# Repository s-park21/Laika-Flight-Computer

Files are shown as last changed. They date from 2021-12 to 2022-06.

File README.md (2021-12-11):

# Liaka-Flight-Computer
Kicad files for the Liaka flight computer

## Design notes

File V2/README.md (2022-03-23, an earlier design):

# Liaka-Flight-Computer
Kicad PCB files for the Liaka flight computer

PCB Ordering Information:

Export the PCB files as Gerber. See online tutorial for details. Upload drill files, gerber files, BOM and .pos file to JLCPCB for PCB manufacture and assembly. 
JLC can assemble most of the components other than RFM95W, GPS, Baro and various other minor parts. I highly reccomend to have JLC assemble the ESP32 chip for you.

For code to run on the board, see my rocket-software repository.

Errata List:

- PWR and GND for XT-30 connector are reversed. 
- Round edges of PCB to minimise stress concentrations.

Areas for improvement:
- MPU6050 locks out after 15g. Consider higher range accelerometer.
- Consider the use of a flash chip rather than a micro SD card.

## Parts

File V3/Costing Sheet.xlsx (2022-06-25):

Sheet: Sheet1
Comment | Designator | Footprint | LCSC | Mouser | Digikey | Cost Each (AUD) | USD to AUD Rate
100nF | C1,C2,C4,C13,C16 | Capacitor_SMD:C_0603_1608Metric | C14663 |  |  | PCB inc. | 1.42
1uF | C11,C12 | Capacitor_SMD:C_0603_1608Metric | C15849 |  |  | PCB inc.
10nF | C17 | Capacitor_SMD:C_0603_1608Metric | C57112 |  |  | PCB inc.
0.1uF | C7,C10,C18,C20 | Capacitor_SMD:C_0603_1608Metric | C14663 |  |  | PCB inc.
2.2nF | C19 | Capacitor_SMD:C_0603_1608Metric | C1604 |  |  | PCB inc.
10uF | C3,C5,C9,C14 | Capacitor_SMD:C_0603_1608Metric | C19702 |  |  | PCB inc.
10uF | C6 | Capacitor_Tantalum_SMD:CP_EIA-3216-18_Kemet-A | C8545 |  |  | PCB inc.
100uF | C8,C15 | Capacitor_Tantalum_SMD:CP_EIA-3528-21_Kemet-B | C16133 |  |  | PCB inc.
LED_BLUE | D1 | LED_SMD:LED_0603_1608Metric | C72041 |  |  | PCB inc.
B5819W | D2,D3,D4 | Diode_SMD:D_SOD-123 | C8598 |  |  | PCB inc.
ERROR_STATUS_LED | D5 | LED_SMD:LED_0603_1608Metric | C2286 |  |  | PCB inc.
LED_RED | D6 | LED_SMD:LED_0603_1608Metric | C72043 |  |  | PCB inc.
XTSD04GLGEAG | IC1 | SON127P800X600X95-8N | C558839 |  |  | 6.07902
Conn_Coaxial | J1 | Connector_Coaxial:SMA_Amphenol_132291_Vertical | C504007 |  |  | 0.63261
2-3S_LiPo_LARGE_HOLE_XT-30 | J2 | Connector_AMASS:AMASS_XT30PW-M_1x02_P2.50mm_Horizontal
USB_B_Micro | J5 | Connector_USB:USB_Micro-B_Molex-105017-0001 | C132563 |  |  | 2.4424
THD2528-11SD-GF | J7 | Local_footprints:THD252811SDGF | C283232 |  |  | 0.30743
SMT-1127-S-R | LS1 | XDCR_SMT-1127-S-R |  | 665-SMT1127SR |  | 2.17
Si2301CDS | Q1,Q2,Q3 | Package_TO_SOT_SMD:SOT-23 | C10487 |  |  | PCB inc.
MMBT2222 | Q4,Q5 | Package_TO_SOT_SMD:SOT-23 | C8512 |  |  | PCB inc.
2N7002 | Q6 | Package_TO_SOT_SMD:SOT-23 | C8545 |  |  | PCB inc.
1k | R1,R13,R14,R18 | Resistor_SMD:R_0603_1608Metric | C21190 |  |  | PCB inc.
12k | R10,R11 | Resistor_SMD:R_0603_1608Metric | C22790 |  |  | PCB inc.
10k | R12,R15,R21 | Resistor_SMD:R_0603_1608Metric | C25804 |  |  | PCB inc.
2.4k | R16,R17 | Resistor_SMD:R_0603_1608Metric | C22940 |  |  | PCB inc.
300k | R19 | Resistor_SMD:R_0603_1608Metric | C23024 |  |  | PCB inc.
50k | R2 | Resistor_SMD:R_0603_1608Metric | C23206 |  |  | PCB inc.
5.1M | R3 | Resistor_SMD:R_0603_1608Metric | C13320 |  |  | PCB inc.
3M | R4,R6 | Resistor_SMD:R_0603_1608Metric | C23156 |  |  | PCB inc.
100k | R5,R8,R9,R20 | Resistor_SMD:R_0603_1608Metric | C25803 |  |  | PCB inc.
1M | R7 | Resistor_SMD:R_0603_1608Metric | C22935 |  |  | PCB inc.
SW_SPDT | SW1 | Local_footprints:SSSS811101 | C109335 |  |  | PCB inc.
RST | SW2 | Button_Switch_SMD:SW_Push_1P1T_NO_CK_KSC6xxJ | C318884 |  |  | PCB inc.
BOOT | SW3 | Button_Switch_SMD:SW_Push_1P1T_NO_CK_KSC6xxJ | C318884 |  |  | PCB inc.
SD_DUMP | SW4 | Button_Switch_SMD:SW_Push_1P1T_NO_CK_KSC6xxJ | C318884 |  |  | PCB inc.
L80-M39 | U1 | Local_footprints:L80-M39 | C133488 |  |  | 25.0914
MPU-6050 | U10 | Local_footprints:MPU-6050 | C24112 |  |  | PCB inc.
MS561101BA03-50 | U2 | Local_footprints:MS561101BA03-50 |  |  | MS561101BA03-50 | 20.72
ADXL375BCCZ-RL7 | U3 | Local_footprints:ADXL375BCCZ-RL7 | C481898 |  |  | 24.4098
RFM95W-915S2 | U4 | RF_Module:HOPERF_RFM9XW_SMD | C2844473 |  |  | 8.48734
LM393 | U5 | Local_footprints:LM393DR2G | C7955 |  |  | 0.0994
ADR5040ARTZ-2.048 | U6 | Local_footprints:Analog_Devices-ADR5040ARTZ-REEL7-Level_C | C144273 |  |  | 1.444282
AMS1117-3.3 | U7 | Package_TO_SOT_SMD:SOT-223-3_TabPin2 | C6186 |  |  | PCB inc.
CP2102N-A01-GQFN28 | U8 | Package_DFN_QFN:QFN-28-1EP_5x5mm_P0.5mm_EP3.35x3.35mm | C6568 |  |  | PCB inc.
ESP32-WROOM-32 | U9 | RF_Module:ESP32-WROOM-32 | C82899 |  |  | PCB inc.
 |  |  | 5 Fully assembled boards
 |  |  |  | PCB Cost |  | 169.03
 |  |  |  | Other component costs |  | 459.41841
 |  |  |  | Total |  | 628.44841
 |  |  | 1 Fully assembled board + 4 partially assembled boards
 |  |  |  | PCB Cost |  | 169.03
 |  |  |  | Other component costs |  | 91.883682
 |  |  |  | Total |  | 260.913682

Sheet: Sheet2
Feature | Laika V2 | Laika V3
GPS | X | X
LoRa | X | X
SD Card | X | X
Flash memory chip |  | X
Accelerometer | X | X
Gyro | X | X
High G Accelerometer |  | X
Buzzer |  | X
Battery protection |  | X
Axes labelled on silk screen |  | X
Barometer | X | X
Can connect to RRC3 | X | X
Looks sexy AF | X | X

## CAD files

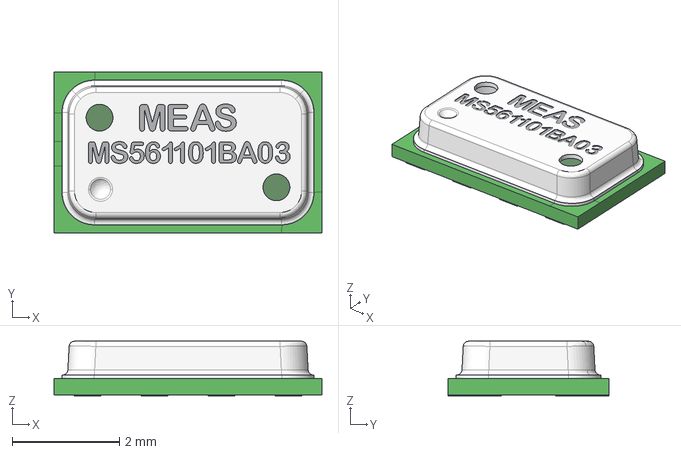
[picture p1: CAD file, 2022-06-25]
V3/Local Library/3D Models/MS5611-01BA03.stp
5.00 x 3.00 x 1.02 mm

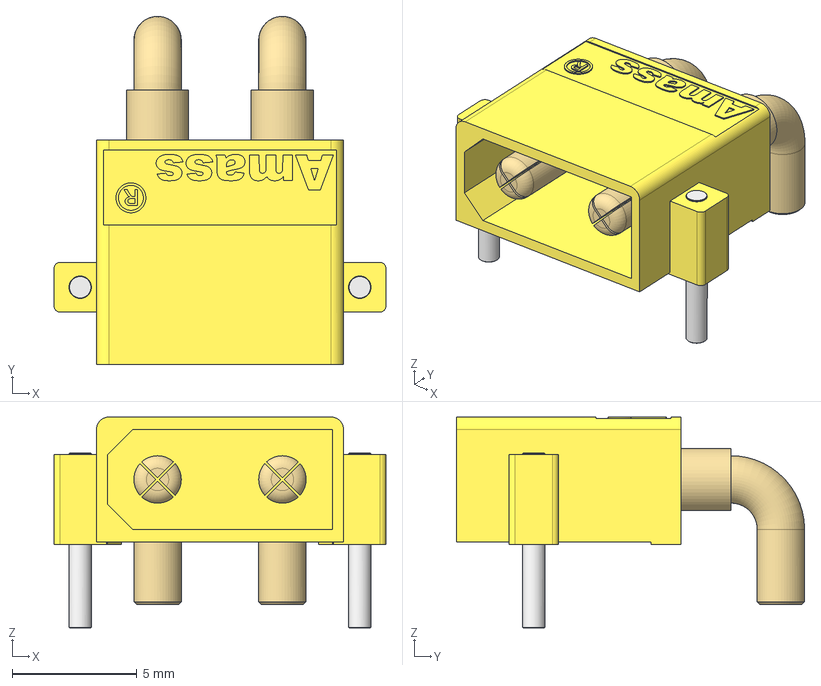
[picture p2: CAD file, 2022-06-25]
V3/Local Library/3D Models/Amass_XT30PW-M.stp
13.3 x 13.9 x 8.45 mm

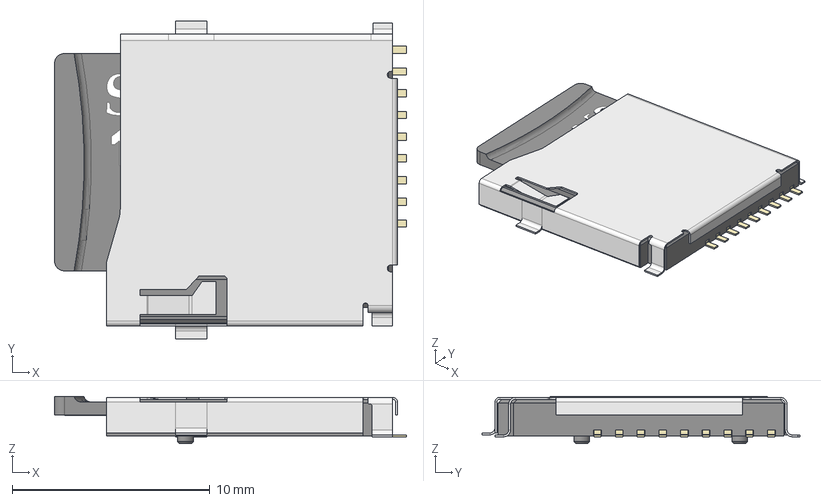
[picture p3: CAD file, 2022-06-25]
V3/Local Library/3D Models/THD2528-11SD-GF.stp.step
17.8 x 16.1 x 2.40 mm

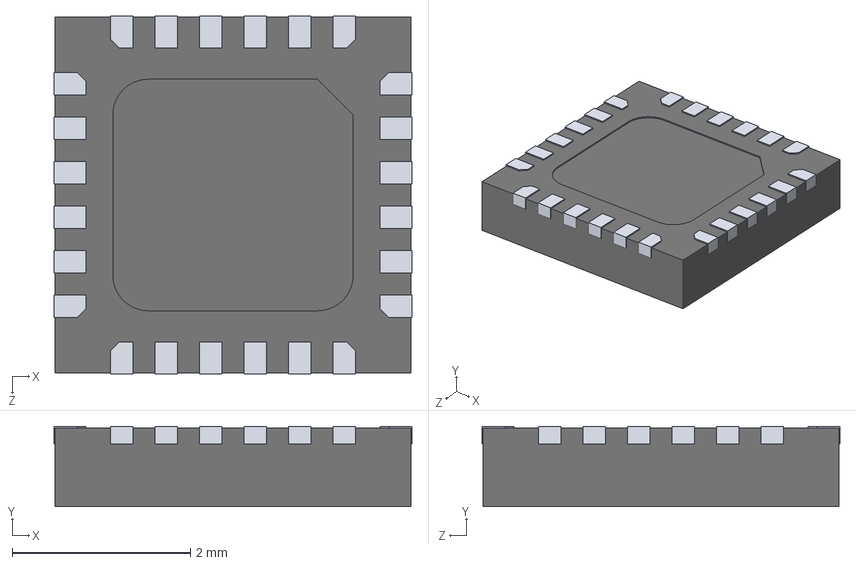
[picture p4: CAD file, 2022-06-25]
V3/Local Library/3D Models/MPU6050.STEP
4.02 x 0.9 x 4.02 mm

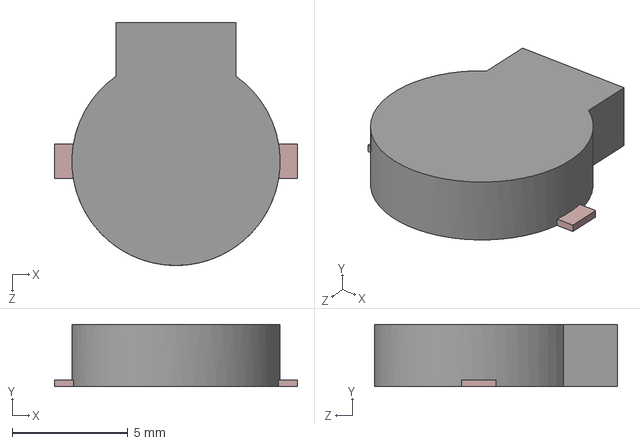
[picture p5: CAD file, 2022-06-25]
V3/Local Library/3D Models/SMT-1127-S-R.step
10.5 x 2.70 x 10.5 mm

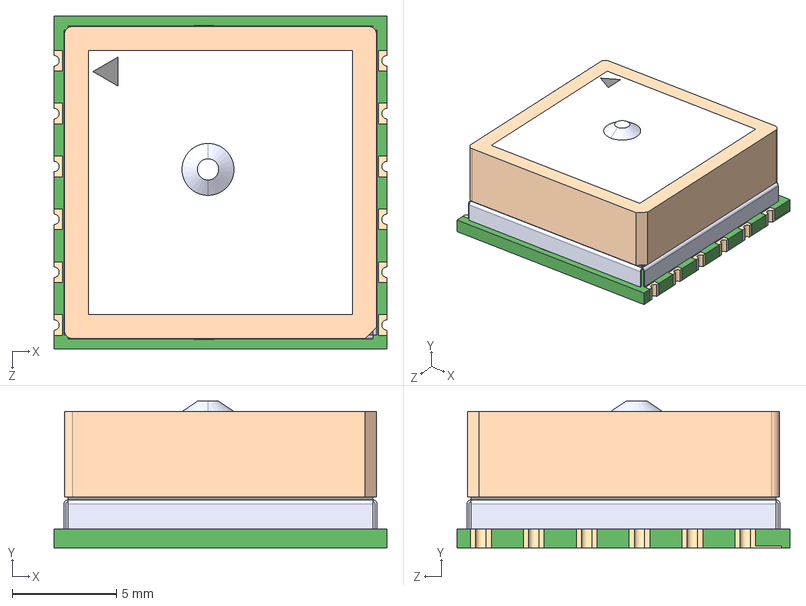
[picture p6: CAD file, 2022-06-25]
V3/Local Library/3D Models/L80-M39.STEP
16.0 x 7.05 x 16.0 mm

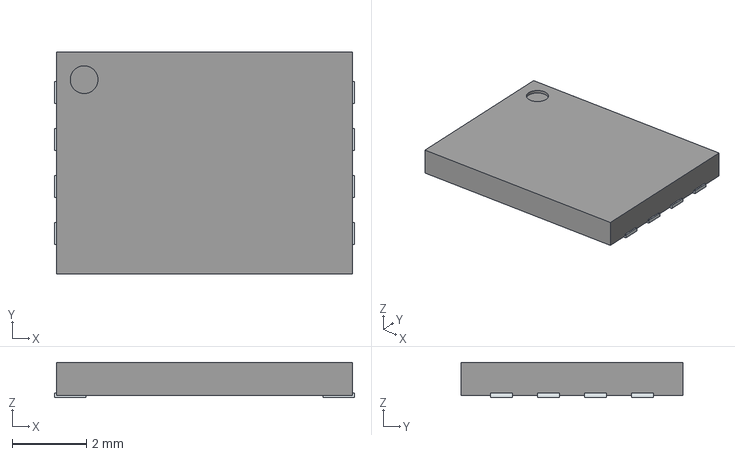
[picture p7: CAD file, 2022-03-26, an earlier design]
V2/Local Library/3D Models/XTSD04GLGEAG.stp
8.10 x 6.00 x 0.95 mm
PinsArrayLR

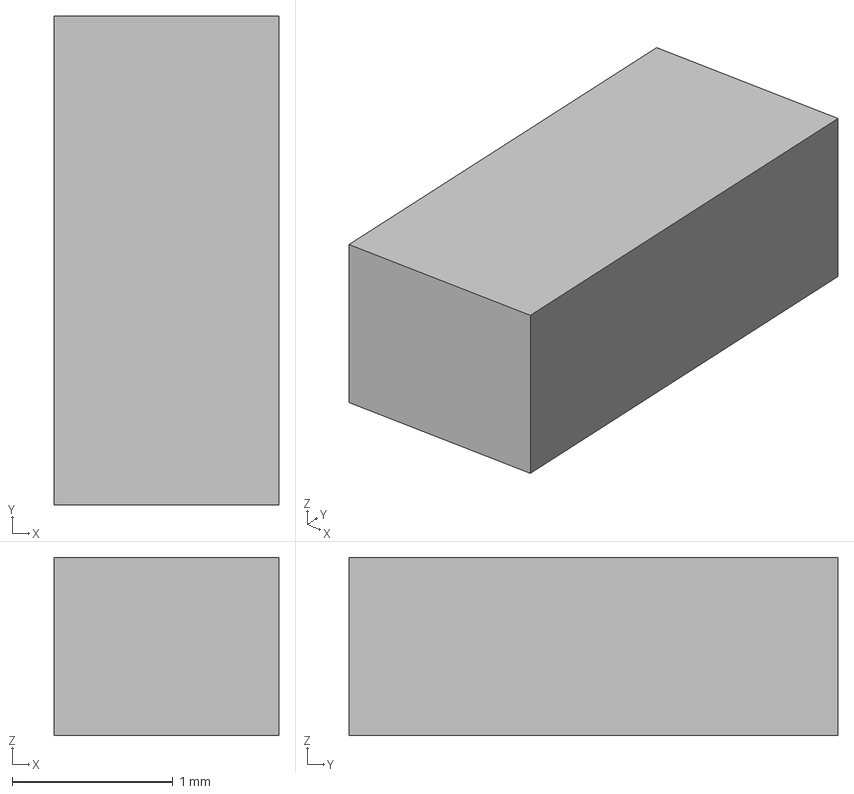
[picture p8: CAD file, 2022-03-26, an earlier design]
V2/Local Library/3D Models/Analog_Devices_-_ADR5040ARTZ-REEL7.step
1.40 x 3.04 x 1.11 mm

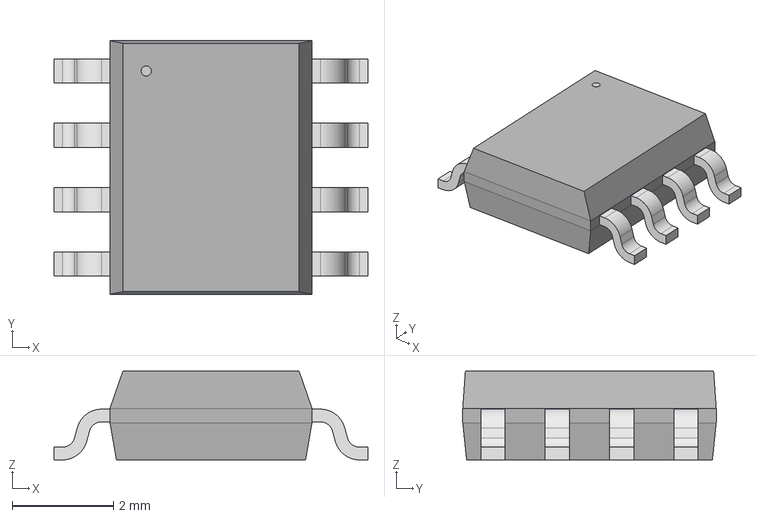
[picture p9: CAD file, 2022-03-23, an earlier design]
V2/Local Library/3D Models/SO_RMN6TP_STM.step
6.20 x 5.00 x 1.75 mm

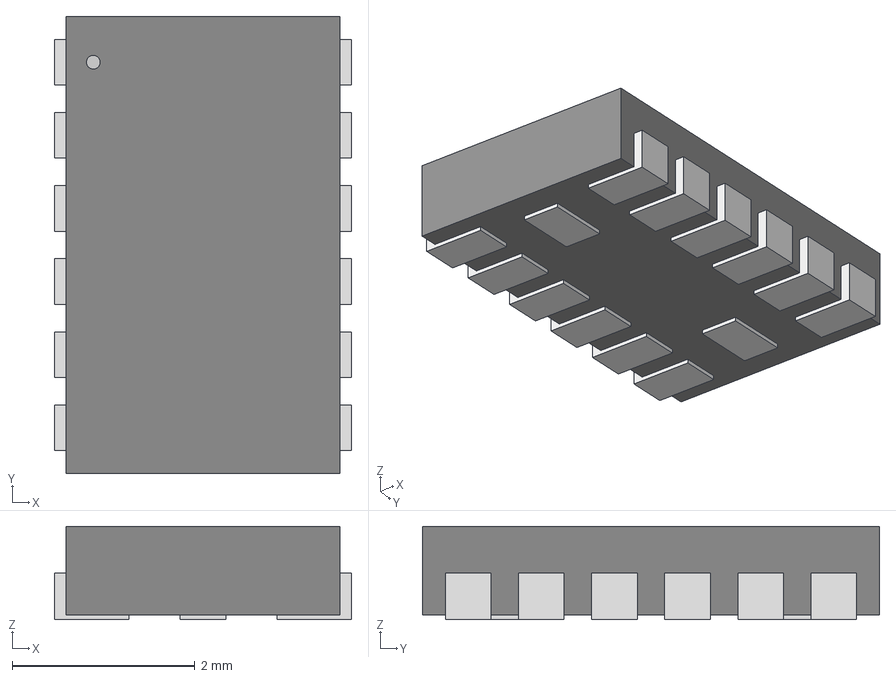
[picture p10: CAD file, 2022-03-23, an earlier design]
V2/Local Library/3D Models/LGA_CC-14-1_ADI.step
3.25 x 5.00 x 1.02 mm

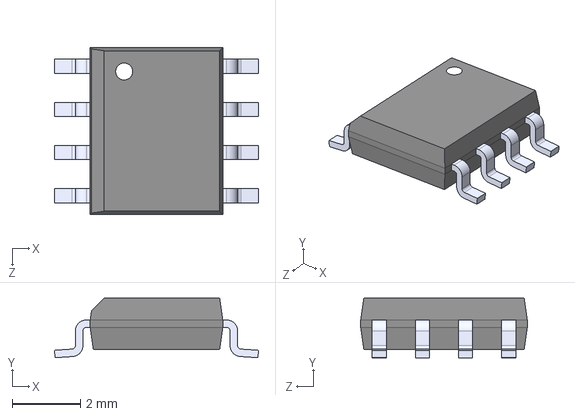
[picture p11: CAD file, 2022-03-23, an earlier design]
V2/Local Library/3D Models/SOIC127P600X175-8N.step
6.00 x 1.75 x 4.90 mm

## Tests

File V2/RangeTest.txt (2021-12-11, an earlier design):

Received packet '1886' with RSSI -23
Received packet '1918' with RSSI -47
Received packet '1949' with RSSI -48
Received packet '1980' with RSSI -48
Received packet '2043' with RSSI -49
Received packet '2074' with RSSI -48
Received packet '2106' with RSSI -48
Received packet '2137' with RSSI -47
Received packet '2200' with RSSI -23
Received packet '2231' with RSSI -22
Received packet '2262' with RSSI -19
Received packet '2325' with RSSI -26
Received packet '2356' with RSSI -19
Received packet '2388' with RSSI -21
Received packet '2419' with RSSI -19
Received packet '2482' with RSSI -19
Received packet '2513' with RSSI -21
Received packet '2544' with RSSI -22
Received packet '2576' with RSSI -23
Received packet '2638' with RSSI -23
Received packet '2670' with RSSI -23
Received packet '2701' with RSSI -23
Received packet '2732' with RSSI -22
Received packet '2795' with RSSI -23
Received packet '2826' with RSSI -47
Received packet '2858' with RSSI -47
Received packet '2889' with RSSI -48
Received packet '2952' with RSSI -49
Received packet '2983' with RSSI -49
Received packet '3014' with RSSI -51
Received packet '3046' with RSSI -51
Received packet '3108' with RSSI -50
Received packet '3140' with RSSI -51
Received packet '3171' with RSSI -49
Received packet '3234' with RSSI -50
Received packet '3265' with RSSI -51
Received packet '3296' with RSSI -55
Received packet '3328' with RSSI -61
Received packet '3390' with RSSI -54
Received packet '3422' with RSSI -52
Received packet '3453' with RSSI -50
Received packet '3484' with RSSI -50
Received packet '3547' with RSSI -45
Received packet '3578' with RSSI -55
Received packet '3610' with RSSI -56
Received packet '3641' with RSSI -58
Received packet '3704' with RSSI -54
Received packet '3735' with RSSI -53
Received packet '3766' with RSSI -55
Received packet '3798' with RSSI -58
Received packet '3860' with RSSI -64
Received packet '3892' with RSSI -66
Received packet '3923' with RSSI -68
Received packet '3986' with RSSI -56
Received packet '4017' with RSSI -59
Received packet '4048' with RSSI -58
Received packet '4080' with RSSI -58
Received packet '4142' with RSSI -58
Received packet '4174' with RSSI -59
Received packet '4205' with RSSI -60
Received packet '4236' with RSSI -64
Received packet '4299' with RSSI -66
Received packet '4330' with RSSI -63
Received packet '4362' with RSSI -64
Received packet '4393' with RSSI -69
Received packet '4456' with RSSI -66
Received packet '4487' with RSSI -63
Received packet '4518' with RSSI -64
Received packet '4550' with RSSI -71
Received packet '4612' with RSSI -64
Received packet '4644' with RSSI -62
Received packet '4675' with RSSI -62
Received packet '4706' with RSSI -62
Received packet '4769' with RSSI -62
Received packet '4800' with RSSI -61
Received packet '4832' with RSSI -59
Received packet '4894' with RSSI -60
Received packet '4926' with RSSI -66
Received packet '4957' with RSSI -77
Received packet '4988' with RSSI -65
Received packet '5051' with RSSI -62
Received packet '5082' with RSSI -61
Received packet '5114' with RSSI -61
Received packet '5145' with RSSI -60
Received packet '5208' with RSSI -61
Received packet '5239' with RSSI -61
Received packet '5270' with RSSI -60
Received packet '5302' with RSSI -61
Received packet '5364' with RSSI -62
Received packet '5396' with RSSI -63
Received packet '5427' with RSSI -63
Received packet '5458' with RSSI -60
Received packet '5521' with RSSI -62
Received packet '5552' with RSSI -61
Received packet '5584' with RSSI -63
Received packet '5646' with RSSI -56
Received packet '5678' with RSSI -61
Received packet '5709' with RSSI -62
Received packet '5740' with RSSI -60
Received packet '5803' with RSSI -63
Received packet '5834' with RSSI -67
Received packet '5866' with RSSI -65
Received packet '5897' with RSSI -63
Received packet '5960' with RSSI -62
Received packet '5991' with RSSI -62
Received packet '6022' with RSSI -61
Received packet '6054' with RSSI -61
Received packet '6116' with RSSI -60
Received packet '6148' with RSSI -60
Received packet '6179' with RSSI -62
Received packet '6210' with RSSI -61
Received packet '6273' with RSSI -60
Received packet '6304' with RSSI -59
Received packet '6336' with RSSI -59
Received packet '6367' with RSSI -60
Received packet '6430' with RSSI -73
Received packet '6461' with RSSI -62
Received packet '6492' with RSSI -58
Received packet '6555' with RSSI -54
Received packet '6586' with RSSI -54
Received packet '6618' with RSSI -58
Received packet '6649' with RSSI -62
Received packet '6711' with RSSI -62
Received packet '6743' with RSSI -59
Received packet '6774' with RSSI -58
Received packet '6806' with RSSI -58
Received packet '6868' with RSSI -59
Received packet '6899' with RSSI -60
Received packet '6931' with RSSI -61
Received packet '6962' with RSSI -62
Received packet '7025' with RSSI -66
Received packet '7056' with RSSI -82
Received packet '7087' with RSSI -69
Received packet '7119' with RSSI -63
Received packet '7181' with RSSI -59
Received packet '7213' with RSSI -58
Received packet '7244' with RSSI -57
Received packet '7307' with RSSI -51
Received packet '7338' with RSSI -58
Received packet '7369' with RSSI -58
Received packet '7401' with RSSI -57
Received packet '7464' with RSSI -57
Received packet '7495' with RSSI -58
Received packet '7526' with RSSI -58
Received packet '7557' with RSSI -58
Received packet '7620' with RSSI -59
Received packet '7651' with RSSI -60
Received packet '7683' with RSSI -63
Received packet '7714' with RSSI -67
Received packet '7777' with RSSI -69
Received packet '7808' with RSSI -68
Received packet '7839' with RSSI -67
Received packet '7871' with RSSI -67
Received packet '7933' with RSSI -65
Received packet '7965' with RSSI -64
Received packet '7996' with RSSI -64
Received packet '8028' with RSSI -64
Received packet '8090' with RSSI -64
Received packet '8121' with RSSI -64
Received packet '8153' with RSSI -64
Received packet '8247' with RSSI -66
Received packet '8278' with RSSI -66
Received packet '8309' with RSSI -67
Received packet '8341' with RSSI -67
Received packet '8372' with RSSI -67
Received packet '8435' with RSSI -67
Received packet '8466' with RSSI -67
Received packet '8498' with RSSI -67
Received packet '8529' with RSSI -67
Received packet '8591' with RSSI -66
Received packet '8623' with RSSI -66
Received packet '8654' with RSSI -65
Received packet '8686' with RSSI -65
Received packet '8748' with RSSI -64
Received packet '8779' with RSSI -65
Received packet '8811' with RSSI -65
Received packet '8842' with RSSI -65
Received packet '8905' with RSSI -65
Received packet '8936' with RSSI -65
Received packet '8967' with RSSI -65
Received packet '8999' with RSSI -65
Received packet '9061' with RSSI -65
Received packet '9093' with RSSI -65
Received packet '9124' with RSSI -65
Received packet '9187' with RSSI -64
Received packet '9218' with RSSI -64
Received packet '9249' with RSSI -64
Received packet '9281' with RSSI -64
Received packet '9344' with RSSI -64
Received packet '9375' with RSSI -64
Received packet '9406' with RSSI -64
Received packet '9437' with RSSI -64
Received packet '9500' with RSSI -63
Received packet '9532' with RSSI -64
Received packet '9563' with RSSI -64
Received packet '9594' with RSSI -64
Received packet '9657' with RSSI -65
Received packet '9688' with RSSI -66
Received packet '9720' with RSSI -66
Received packet '9751' with RSSI -67
Received packet '9813' with RSSI -69
Received packet '9845' with RSSI -69
Received packet '9876' with RSSI -69
Received packet '9939' with RSSI -58
Received packet '9970' with RSSI -61
Received packet '10001' with RSSI -58
Received packet '10033' with RSSI -53
Received packet '10096' with RSSI -53
Received packet '10127' with RSSI -53
Received packet '10158' with RSSI -54
Received packet '10190' with RSSI -53
Received packet '10252' with RSSI -53
Received packet '10284' with RSSI -53
Received packet '10315' with RSSI -52
Received packet '10378' with RSSI -54
Received packet '10409' with RSSI -54
Received packet '10440' with RSSI -54
Received packet '10503' with RSSI -57
Received packet '10534' with RSSI -58
Received packet '10566' with RSSI -58
Received packet '10597' with RSSI -60
Received packet '10660' with RSSI -61
Received packet '10691' with RSSI -63
Received packet '10722' with RSSI -65
Received packet '10785' with RSSI -70
Received packet '10817' with RSSI -69
Received packet '10848' with RSSI -67
Received packet '10911' with RSSI -57
Received packet '10942' with RSSI -62
Received packet '10973' with RSSI -61
Received packet '11005' with RSSI -60
Received packet '11067' with RSSI -60
Received packet '11099' with RSSI -60
Received packet '11130' with RSSI -60
Received packet '11193' with RSSI -57
Received packet '11224' with RSSI -53
Received packet '11255' with RSSI -52
Received packet '11287' with RSSI -52
Received packet '11349' with RSSI -60
Received packet '11381' with RSSI -58
Received packet '11412' with RSSI -56
Received packet '11475' with RSSI -55
Received packet '11506' with RSSI -55
Received packet '11537' with RSSI -57
Received packet '11600' with RSSI -52
Received packet '11631' with RSSI -59
Received packet '11663' with RSSI -58
Received packet '11694' with RSSI -59
Received packet '11757' with RSSI -59
Received packet '11788' with RSSI -58
Received packet '11820' with RSSI -58
Received packet '11882' with RSSI -57
Received packet '11914' with RSSI -58
Received packet '11945' with RSSI -58
Received packet '11976' with RSSI -58
Received packet '12039' with RSSI -58
Received packet '12070' with RSSI -58
Received packet '12102' with RSSI -59
Received packet '12164' with RSSI -59
Received packet '12196' with RSSI -59
Received packet '12227' with RSSI -60
Received packet '12290' with RSSI -60
Received packet '12321' with RSSI -61
Received packet '12352' with RSSI -61
Received packet '12384' with RSSI -62
Received packet '12447' with RSSI -61
Received packet '12478' with RSSI -62
Received packet '12509' with RSSI -61
Received packet '12572' with RSSI -55
Received packet '12603' with RSSI -61
Received packet '12635' with RSSI -61
Received packet '12666' with RSSI -61
Received packet '12729' with RSSI -61
Received packet '12760' with RSSI -61
Received packet '12791' with RSSI -61
Received packet '12854' with RSSI -60
Received packet '12885' with RSSI -61
Received packet '12917' with RSSI -61
Received packet '12979' with RSSI -60
Received packet '13011' with RSSI -61
Received packet '13042' with RSSI -61
Received packet '13073' with RSSI -60
Received packet '13136' with RSSI -60
Received packet '13167' with RSSI -61
Received packet '13199' with RSSI -61
Received packet '13261' with RSSI -61
Received packet '13293' with RSSI -61
Received packet '13324' with RSSI -61
Received packet '13356' with RSSI -61
Received packet '13418' with RSSI -61
Received packet '13450' with RSSI -61
Received packet '13481' with RSSI -61
Received packet '13544' with RSSI -62
Received packet '13575' with RSSI -62
Received packet '13606' with RSSI -62
Received packet '13669' with RSSI -62
Received packet '13700' with RSSI -62
Received packet '13732' with RSSI -63
Received packet '13763' with RSSI -63
Received packet '13826' with RSSI -63
Received packet '13857' with RSSI -63
Received packet '13888' with RSSI -63
Received packet '13951' with RSSI -63
Received packet '13982' with RSSI -63
Received packet '14014' with RSSI -63
Received packet '14045' with RSSI -61
Received packet '14108' with RSSI -59
Received packet '14139' with RSSI -58
Received packet '14171' with RSSI -57
Received packet '14233' with RSSI -53
Received packet '14265' with RSSI -53
Received packet '14296' with RSSI -53
Received packet '14359' with RSSI -59
Received packet '14390' with RSSI -63
Received packet '14421' with RSSI -65
Received packet '14453' with RSSI -62
Received packet '14515' with RSSI -62
Received packet '14547' with RSSI -62
Received packet '14578' with RSSI -61
Received packet '14641' with RSSI -62
Received packet '14672' with RSSI -63
Received packet '14703' with RSSI -65
Received packet '14735' with RSSI -71
Received packet '14797' with RSSI -64
Received packet '14829' with RSSI -61
Received packet '14860' with RSSI -61
Received packet '14923' with RSSI -66
Received packet '14954' with RSSI -67
Received packet '14985' with RSSI -68
Received packet '15048' with RSSI -71
Received packet '15080' with RSSI -73
Received packet '15111' with RSSI -70
Received packet '15142' with RSSI -65
Received packet '15205' with RSSI -64
Received packet '15236' with RSSI -64
Received packet '15268' with RSSI -66
Received packet '15330' with RSSI -71
Received packet '15362' with RSSI -72
Received packet '15393' with RSSI -73
Received packet '15456' with RSSI -64
Received packet '15487' with RSSI -69
Received packet '15518' with RSSI -68
Received packet '15550' with RSSI -67
Received packet '15612' with RSSI -69
Received packet '15644' with RSSI -68
Received packet '15675' with RSSI -66
Received packet '15738' with RSSI -66
Received packet '15769' with RSSI -66
Received packet '15800' with RSSI -66
Received packet '15832' with RSSI -67
Received packet '15895' with RSSI -67
Received packet '15926' with RSSI -67
Received packet '15957' with RSSI -69
Received packet '16020' with RSSI -68
Received packet '16051' with RSSI -68
Received packet '16083' with RSSI -67
Received packet '16145' with RSSI -62
Received packet '16177' with RSSI -68
Received packet '16208' with RSSI -68
Received packet '16239' with RSSI -68
Received packet '16302' with RSSI -70
Received packet '16333' with RSSI -71
Received packet '16365' with RSSI -68
Received packet '16427' with RSSI -69
Received packet '16459' with RSSI -68
Received packet '16490' with RSSI -69
Received packet '16521' with RSSI -68
Received packet '16584' with RSSI -66
Received packet '16615' with RSSI -65
Received packet '16647' with RSSI -65
Received packet '16709' with RSSI -65
Received packet '16741' with RSSI -65
Received packet '16772' with RSSI -64
Received packet '16835' with RSSI -64
Received packet '16866' with RSSI -63
Received packet '16898' with RSSI -64
Received packet '16929' with RSSI -65
Received packet '16992' with RSSI -67
Received packet '17023' with RSSI -70
Received packet '17054' with RSSI -73
Received packet '17117' with RSSI -72
Received packet '17148' with RSSI -71
Received packet '17180' with RSSI -68
Received packet '17211' with RSSI -67
Received packet '17274' with RSSI -66
Received packet '17305' with RSSI -66
Received packet '17336' with RSSI -65
Received packet '17399' with RSSI -63
Received packet '17430' with RSSI -63
Received packet '17462' with RSSI -64
Received packet '17524' with RSSI -64
Received packet '17556' with RSSI -64
Received packet '17587' with RSSI -63
Received packet '17618' with RSSI -62
Received packet '17681' with RSSI -63
Received packet '17713' with RSSI -65
Received packet '17744' with RSSI -66
Received packet '17807' with RSSI -70
Received packet '17838' with RSSI -70
Received packet '17869' with RSSI -68
Received packet '17901' with RSSI -66
Received packet '17963' with RSSI -64
Received packet '17995' with RSSI -63
Received packet '18026' with RSSI -64
Received packet '18089' with RSSI -59
Received packet '18120' with RSSI -67
Received packet '18151' with RSSI -72
Received packet '18214' with RSSI -74
Received packet '18245' with RSSI -70
Received packet '18277' with RSSI -67
Received packet '18308' with RSSI -66
Received packet '18371' with RSSI -71
Received packet '18402' with RSSI -76
Received packet '18433' with RSSI -76
Received packet '18496' with RSSI -71
Received packet '18528' with RSSI -69
Received packet '18559' with RSSI -69
Received packet '18590' with RSSI -69
Received packet '18653' with RSSI -66
Received packet '18684' with RSSI -68
Received packet '18716' with RSSI -73
Received packet '18778' with RSSI -74
Received packet '18810' with RSSI -70
Received packet '18841' with RSSI -68
Received packet '18904' with RSSI -67
Received packet '18935' with RSSI -66
Received packet '18966' with RSSI -65
Received packet '18998' with RSSI -64
Received packet '19060' with RSSI -66
Received packet '19092' with RSSI -67
Received packet '19123' with RSSI -65
Received packet '19186' with RSSI -66
Received packet '19217' with RSSI -66
Received packet '19248' with RSSI -65
Received packet '19280' with RSSI -66
Received packet '19342' with RSSI -73
Received packet '19374' with RSSI -79
Received packet '19405' with RSSI -70
Received packet '19468' with RSSI -68
Received packet '19499' with RSSI -71
Received packet '19531' with RSSI -69
Received packet '19593' with RSSI -63
Received packet '19625' with RSSI -62
Received packet '19656' with RSSI -62
Received packet '19687' with RSSI -64
Received packet '19750' with RSSI -74
Received packet '19781' with RSSI -75
Received packet '19813' with RSSI -77
Received packet '19875' with RSSI -72
Received packet '19907' with RSSI -68
Received packet '19938' with RSSI -64
Received packet '19969' with RSSI -63
Received packet '20032' with RSSI -65
Received packet '20063' with RSSI -65
Received packet '20095' with RSSI -64
Received packet '20157' with RSSI -62
Received packet '20189' with RSSI -62
Received packet '20220' with RSSI -63
Received packet '20283' with RSSI -66
Received packet '20314' with RSSI -68
Received packet '20346' with RSSI -69
Received packet '20377' with RSSI -71
Received packet '20440' with RSSI -69
Received packet '20471' with RSSI -66
Received packet '20502' with RSSI -65
Received packet '20565' with RSSI -64
Received packet '20596' with RSSI -61
Received packet '20628' with RSSI -60
Received packet '20690' with RSSI -58
Received packet '20722' with RSSI -68
Received packet '20753' with RSSI -66
Received packet '20784' with RSSI -64
Received packet '20847' with RSSI -64
Received packet '20878' with RSSI -63
Received packet '20910' with RSSI -65
Received packet '20972' with RSSI -69
Received packet '21004' with RSSI -68
Received packet '21035' with RSSI -69
Received packet '21066' with RSSI -70
Received packet '21129' with RSSI -68
Received packet '21161' with RSSI -68
Received packet '21192' with RSSI -69
Received packet '21255' with RSSI -71
Received packet '21286' with RSSI -73
Received packet '21317' with RSSI -76
Received packet '21380' with RSSI -91
Received packet '21411' with RSSI -80
Received packet '21443' with RSSI -74
Received packet '21474' with RSSI -71
Received packet '21537' with RSSI -67
Received packet '21568' with RSSI -66
Received packet '21599' with RSSI -65
Received packet '21662' with RSSI -66
Received packet '21693' with RSSI -65
Received packet '21725' with RSSI -67
Received packet '21756' with RSSI -69
Received packet '21819' with RSSI -72
Received packet '21850' with RSSI -76
Received packet '21881' with RSSI -79
Received packet '21944' with RSSI -71
Received packet '21975' with RSSI -70
Received packet '22007' with RSSI -71
Received packet '22070' with RSSI -75
Received packet '22101' with RSSI -72
Received packet '22132' with RSSI -70
Received packet '22164' with RSSI -71
Received packet '22226' with RSSI -71
Received packet '22258' with RSSI -74
Received packet '22289' with RSSI -78
Received packet '22352' with RSSI -76
Received packet '22383' with RSSI -75
Received packet '22414' with RSSI -75
Received packet '22446' with RSSI -75
Received packet '22508' with RSSI -70
Received packet '22540' with RSSI -70
Received packet '22571' with RSSI -72
Received packet '22634' with RSSI -69
Received packet '22665' with RSSI -70
Received packet '22696' with RSSI -72
Received packet '22759' with RSSI -70
Received packet '22790' with RSSI -71
Received packet '22822' with RSSI -70
Received packet '22853' with RSSI -67
Received packet '22916' with RSSI -70
Received packet '22947' with RSSI -69
Received packet '22979' with RSSI -69
Received packet '23041' with RSSI -75
Received packet '23073' with RSSI -73
Received packet '23104' with RSSI -74
Received packet '23135' with RSSI -80
Received packet '23198' with RSSI -77
Received packet '23229' with RSSI -73
Received packet '23261' with RSSI -71
Received packet '23323' with RSSI -71
Received packet '23355' with RSSI -73
Received packet '23386' with RSSI -74
Received packet '23449' with RSSI -78
Received packet '23480' with RSSI -78
Received packet '23511' with RSSI -75
Received packet '23543' with RSSI -75
Received packet '23605' with RSSI -78
Received packet '23637' with RSSI -75
Received packet '23668' with RSSI -73
Received packet '23731' with RSSI -78
Received packet '23762' with RSSI -75
Received packet '23794' with RSSI -75
Received packet '23825' with RSSI -76
Received packet '23888' with RSSI -76
Received packet '23919' with RSSI -76
Received packet '23950' with RSSI -80
Received packet '24013' with RSSI -75
Received packet '24044' with RSSI -74
Received packet '24076' with RSSI -76
Received packet '24138' with RSSI -81
Received packet '24170' with RSSI -79
Received packet '24201' with RSSI -80
Received packet '24232' with RSSI -86
Received packet '24295' with RSSI -76
Received packet '24326' with RSSI -76
Received packet '24358' with RSSI -78
Received packet '24420' with RSSI -78
Received packet '24452' with RSSI -80
Received packet '24483' with RSSI -77
Received packet '24514' with RSSI -75
Received packet '24577' with RSSI -75
Received packet '24609' with RSSI -78
Received packet '24640' with RSSI -87
Received packet '24703' with RSSI -97
Received packet '24734' with RSSI -82
Received packet '24765' with RSSI -79
Received packet '24828' with RSSI -88
Received packet '24859' with RSSI -79
Received packet '24891' with RSSI -74
Received packet '24922' with RSSI -72
Received packet '24985' with RSSI -71
Received packet '25016' with RSSI -71
Received packet '25047' with RSSI -74
Received packet '25110' with RSSI -73
Received packet '25141' with RSSI -73
Received packet '25173' with RSSI -72
Received packet '25235' with RSSI -64
Received packet '25267' with RSSI -69
Received packet '25298' with RSSI -69
Received packet '25329' with RSSI -69
Received packet '25392' with RSSI -69
Received packet '25423' with RSSI -69
Received packet '25455' with RSSI -70
Received packet '25518' with RSSI -69
Received packet '25549' with RSSI -69
Received packet '25580' with RSSI -70
Received packet '25612' with RSSI -71
Received packet '25674' with RSSI -69
Received packet '25706' with RSSI -68
Received packet '25737' with RSSI -69
Received packet '25800' with RSSI -71
Received packet '25831' with RSSI -71
Received packet '25862' with RSSI -70
Received packet '25925' with RSSI -65
Received packet '25956' with RSSI -71
Received packet '25988' with RSSI -73
Received packet '26019' with RSSI -72
Received packet '26082' with RSSI -69
Received packet '26113' with RSSI -70
Received packet '26144' with RSSI -72
Received packet '26207' with RSSI -69
Received packet '26239' with RSSI -69
Received packet '26270' with RSSI -70
Received packet '26301' with RSSI -70
Received packet '26364' with RSSI -70
Received packet '26395' with RSSI -67
Received packet '26427' with RSSI -69
Received packet '26489' with RSSI -68
Received packet '26521' with RSSI -69
Received packet '26552' with RSSI -71
Received packet '26615' with RSSI -74
Received packet '26646' with RSSI -74
Received packet '26677' with RSSI -74
Received packet '26709' with RSSI -73
Received packet '26771' with RSSI -69
Received packet '26803' with RSSI -66
Received packet '26834' with RSSI -67
Received packet '26897' with RSSI -68
Received packet '26928' with RSSI -68
Received packet '26959' with RSSI -67
Received packet '26991' with RSSI -68
Received packet '27053' with RSSI -69
Received packet '27085' with RSSI -70
Received packet '27116' with RSSI -70
Received packet '27179' with RSSI -71
Received packet '27210' with RSSI -71
Received packet '27242' with RSSI -70
Received packet '27304' with RSSI -72
Received packet '27336' with RSSI -73
Received packet '27367' with RSSI -74
Received packet '27398' with RSSI -73
Received packet '27461' with RSSI -70
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

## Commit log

2021-12-11 Added: all files for Liaka V2
    [JLC_Order_BOM.xlsx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]
2022-03-23 Added new version of FC and restructured folders
    [ESP32.kicad_sch, JLC_Order_BOM.xlsx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]
2022-03-23 Changed imu added flash chip
    [DataLogging.kicad_sch, ESP32.kicad_sch, JLC_Order_BOM.xlsx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]
2022-03-26 Added sims, updated V3 board
    [Analog_Devices_-_ADR5040ARTZ-REEL7.step, DataLogging.kicad_sch, ESP32.kicad_sch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]
2022-03-28 Added mpu6050 back
    [ESP32.kicad_sch, Liaka_V3.kicad_pcb, Liaka_V3.kicad_sch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]
2022-03-28 buzzer added
    [ESP32.kicad_sch, Liaka_V3.kicad_sch, Power.kicad_sch]
2022-03-28 almost finished component placement
    [DataLogging.kicad_sch, ESP32.kicad_sch, Liaka_V3.kicad_pcb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]
2022-04-30 Updated costing sheet:
    [Amass_XT30PW-M.stp, Analog_Devices_-_ADR5040ARTZ-REEL7.step, Costing Sheet.xlsx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]
2022-09-15 Switched orentation of LVCO P-ch mosfet
    [Power.kicad_sch]
2022-09-29 Added comments for req changes
    [Sensors.kicad_sch]
2022-10-16 New parts placed and routed
    [ESP32.kicad_sch, Liaka_V3.kicad_pcb, Liaka_V3.kicad_sch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]
2022-12-11 Added reccomended changes for V3
    [Liaka_V3.kicad_sch, Power.kicad_sch, Sensors.kicad_sch]
2023-04-03 added MPN to BOM
    [L2_board.csv]
